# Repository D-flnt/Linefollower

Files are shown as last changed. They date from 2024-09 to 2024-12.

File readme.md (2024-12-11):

# LineFollower Daan Flinterman 3AMA 2024

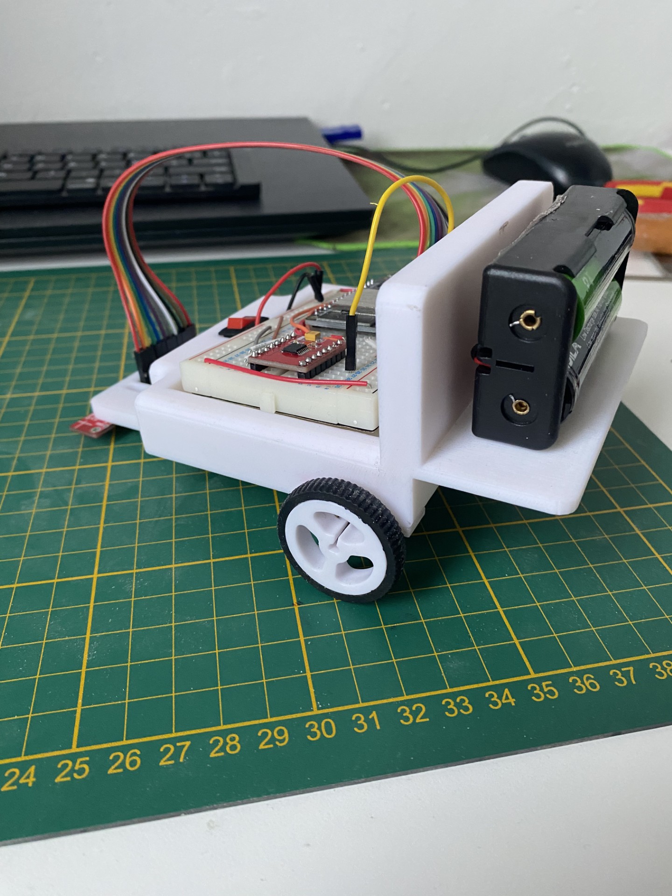
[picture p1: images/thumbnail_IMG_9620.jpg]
Mijn linefollower

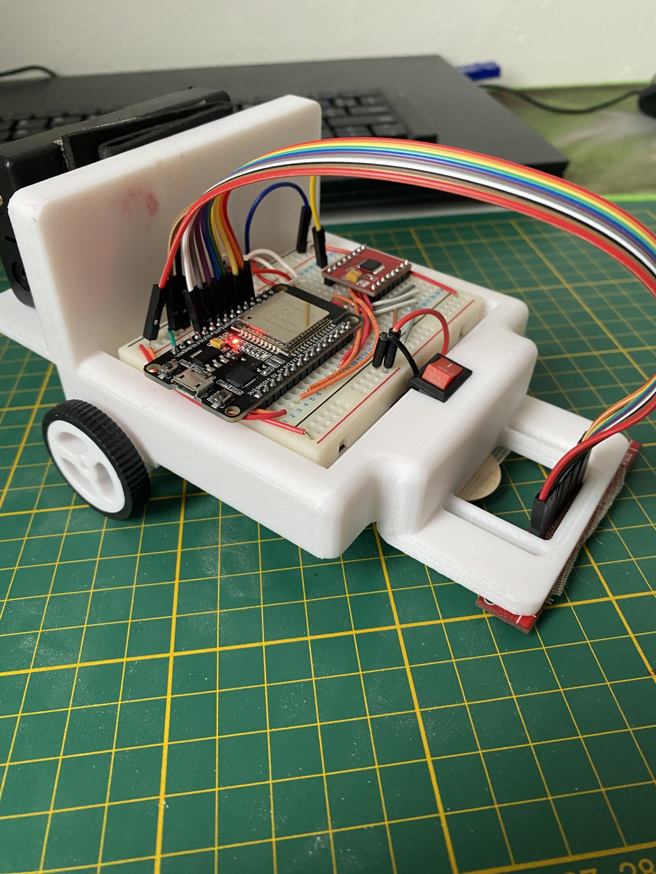
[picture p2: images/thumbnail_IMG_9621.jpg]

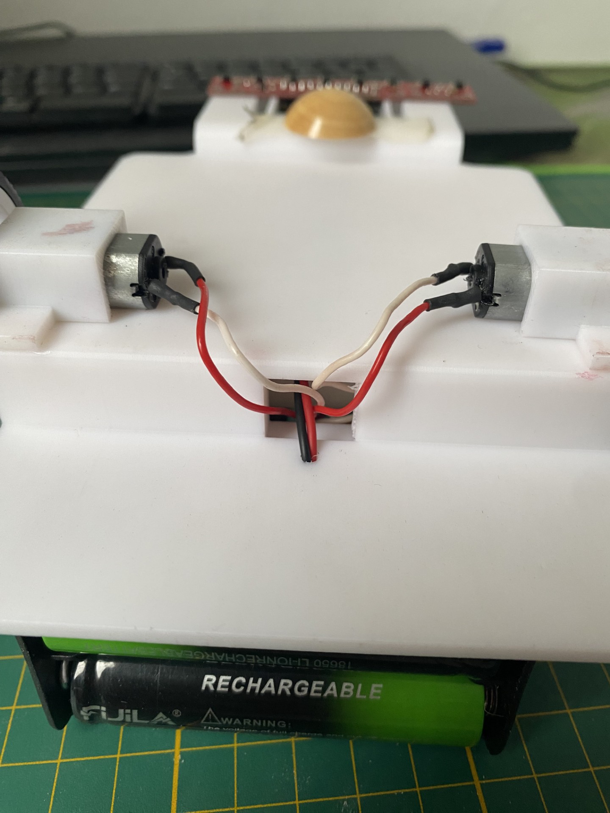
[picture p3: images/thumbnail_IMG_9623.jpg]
Onderzijde


## specifications

microcontroller: ESP32

motors: Micro Metal Gearmotor 50:1

h-bridge: DRV8833

sensors: QTR-8A Sensor Array

batteries: 2 x 18650 Li-Ion

wireless communication: Internal bluetooth module (ESP-32)

distance sensor - motors: 108mm

weight:316g

speed: 0,42m/s

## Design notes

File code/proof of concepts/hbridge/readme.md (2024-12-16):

# H-Bridge proof of concept

Minimale hard- & software die aantoont dat 2 motoren onafhankelijk van elkaar kunnen draaien, en (traploos) regelbaar zijn in snelheid en draairichting.

### Stappen:
1. Sluit de motoren aan volgens schema (OUT1, OUT2 voor motor 1, OUT3, OUT4 voor motor 2).
2. Sluit de ingangen van de H-brug volgens het schema voorzien in deze repository.
3. Sluit de **STBY** pin aan op de 3.3 V pin van de ESP-32.
4. Sluit **VCC**, **GND**, en **VM** aan volgens het schema.
5. Upload het programma en kijk of de motoren op verschillende sneleden en richtingen draaien.

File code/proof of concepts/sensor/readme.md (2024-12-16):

# Sensoren proof of concept

Minimale hard- en software die aantoont dat minimaal 6 sensoren onafhankelijk van elkaar kunnen uitgelezen worden (geen calibratie, normalisatie of interpolatie). Hierbij moet een zo groot mogelijk bereik van de AD converter benut worden (indien van toepassing).

### Stappen:
1. Zorg voor een **ESP32** en een **QTR-8 Sensor**.
2. Sluit de **VCC** pin van de sensor aan op **3.3V** van de ESP32.
3. Sluit de **GND** pin van de sensor aan op de **GND** van de ESP32.
4. Sluit de pinnen van de sensor aan volgens het schema voorzien in deze repository met de ESP 32.
5. Voorzie de ESP32 van spanning.
6. Upload het programma naar de ESP32.
7. Kijk in de seriële monitor (debugger) je zou hier de waardes van de sensoren moeten zien en de waardes zouden moeten veranderen als je je vinger voor de sensoren beweegt.

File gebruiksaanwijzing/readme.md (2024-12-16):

# Gebruiksaanwijzing

# Gebruiksaanwijzing

### opladen / vervangen batterijen
Ik heb hiervoor een oplader gekocht van aliexpress speciaal voor het type 18650 batterijen.
Maakt gebruik van een USB micro aansluiting.

### draadloze communicatie
#### verbinding maken **!ALLEEN MOGELIJK MET ANDROID**
Ik gebruik de app "serial bluetooth" met 10k reviews in de play store.
Je moet eerst in het programma declareren dat de bluetooth wordt opgestart. Hier zal je ook een naam geven aan je bluetooth module.
Als dit gebeurt is dan voorzie je de ESP-32 van stroom.
Dan verbindt je via instellingen van je android met de gegeven naam van de ESP-32.
Dan open je de APP serial bluetooth en druk je op new connection, hier duidt je weer je esp 32 aan.
Normaal gezien komt er in de terminal "connected" te staan.
Je kan nu commando's doorsturen.

#### commando's
- getPID: Vraag de huidige P, I en D waarde op.
- start: Laat de robot rijden.
- stop: Stopt de robot.
- baseSpeed[0..255]: Pas de basissnelheid aan (bij een rechte lijn)
- maxSpeed[0..255]: Pas de maximale snelheid aan (om bij te sturen)
- kp[0..]: Pas de Proportionele waarde aan.
- Ki[0..]: Pas de Integrerende waarde aan.
- Kd[0..]: Pas de Differentiërende waarde aan.

### settings
De robot rijdt stabiel met volgende parameters:
- Base speed: 95
- Max speed: 140
- Kp: 19
- Ki: 0
- Kd: 10

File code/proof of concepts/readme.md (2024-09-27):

# Proof of Concepts

Een proof of concept is een combinatie van minimale hard- en software om eenvoudig aan te tonen dat iets werkt.  
Proof of concepts kunnen enerzijds als eerste poging dienen om een bepaald onderdeel van het project werkend te krijgen. Anderzijds kunnen ze tijdens het debuggen van het finale project dienen als test om eventuele hardware problemen te elimineren bij onduidelijke problemen.
<br />  
<br />
Een proof of concept bestaat uit
* een elektronisch schema (indien van toepassing)
* minimale code om de voorop gestelde zaken te demonstreren
* minimale uitleg / aandachtspunten
<br />
De elektronische schakelingen van de proof of concepts komen bij voorkeur overeen met deze van de uiteindelijke linefollower, zodat de code zonder aanpassingen op het finale project kan draaien.

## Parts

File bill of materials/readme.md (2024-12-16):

## bill of materials
<br />

|volgnummer|naam|omschrijving|nieuw/recup|kostprijs/stuk|aantal|subtotaal|
|---|----|---|---|---|---|---|
| 1| QTR-8A Reflectance Sensor Array | This sensor module has 8 IR LED/phototransistor pairs mounted on a 0.375" pitch, making it a great detector for a line-following robot. Pairs of LEDs are arranged in series to halve current consumption, and a MOSFET allows the LEDs to be turned off for additional sensing or power-savings options. Each sensor provides a separate analog voltage output. | Nieuw | €9,95/piece | 1 | €9.95 |
| 2| Micro Metal Gear motor 1:50  | Mini N20 Reductiemotor DC 3 V-6 V 330 RPM Groot Koppel Volledig Metalen Versnellingsbak Reductiemotor 1:50 Reductieverhouding Vingerafdrukslot | Nieuw | €1.34/piece | 2  | €2,68 | 
| 3|  18650 Li-Ion battery | 2 batterijen in serie leveren bijna 8 volt. Hiermee voed ik de H-brug en de Microcontroller. | Nieuw | €2,02/piece | 2 | €4,08 |
| 4| DRV8833 H-Brug | Zal afhangend van de ingang signalen de motoren aansturen met de spanning van de batterijen. We gebruiken een H brug omdat deze makkelijker meer vermogen kan schakelen dan de Microcontroller zelf. |  Nieuw | €1,79/piece |  1 | €1,79 |
| 5| 18650 Batterij houder | Zorgt ervoor dat ik de spanning van de batterijen in serie op mn breadboard kan zetten. |  Nieuw | €1,39/piece |  1 | €1,39 |
| 6|  Tuimelschakelaar 3A  |  Een bistabiele schakelaar om de spanning van de batterijen naar het breadboard te onderbreken. | Nieuw | €0,18/piece | 10 | €1,80 |
| 7| 18650 Batterij oplader (2 sleufs) | Voor de batterijen op te laden | Nieuw | €1,92/piece | 1 |  €1.92 |
| 8|  D Gat wielen  | D gat wielen die perfect passen op de as van de reductie motor. | Nieuw | €0,39/piece |  10 | €3,89  |
| 9|  ESP-32 WROOM  | Brein van de lijnvolger (bluetooh en wifi compatable) | Nieuw | €10,00/piece | 1 | €10,00 |
| 10|  Chaussis Auto (3D printed)  |  Zorgt ervoor dat alle componenten bij elkaar worden gehouden. | Nieuw | €0,00/piece | 1 | €0,00 |
| 11| Breadboard (456 pins) | Soldeerloos breadboard om makkelijk connecties te maken tussen de componenten. | Nieuw | €9,95/piece |  1 | €9,95 |
| 12| | | | | | |

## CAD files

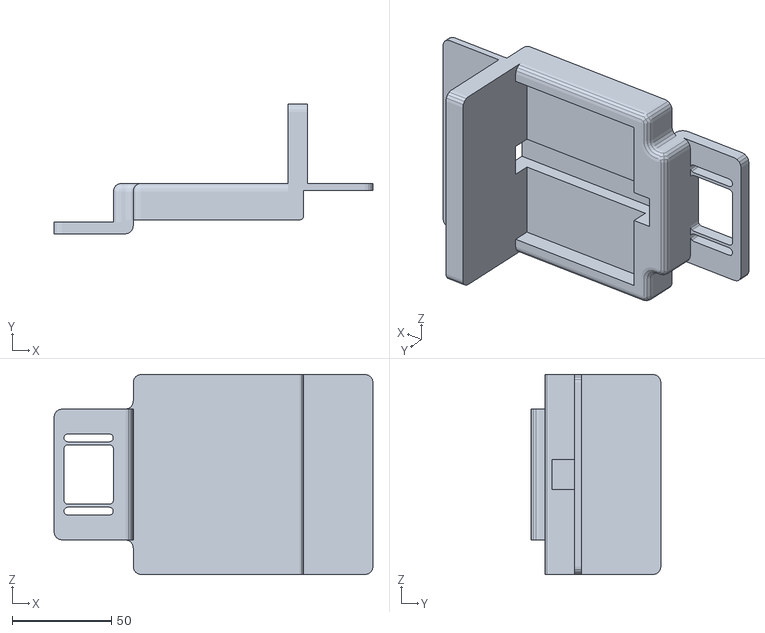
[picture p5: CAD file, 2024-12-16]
technische tekeningen/mechanisch/frame_karretje.stl
161.0 x 65.5 x 101.0

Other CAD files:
technische tekeningen/mechanisch/frame.ipt

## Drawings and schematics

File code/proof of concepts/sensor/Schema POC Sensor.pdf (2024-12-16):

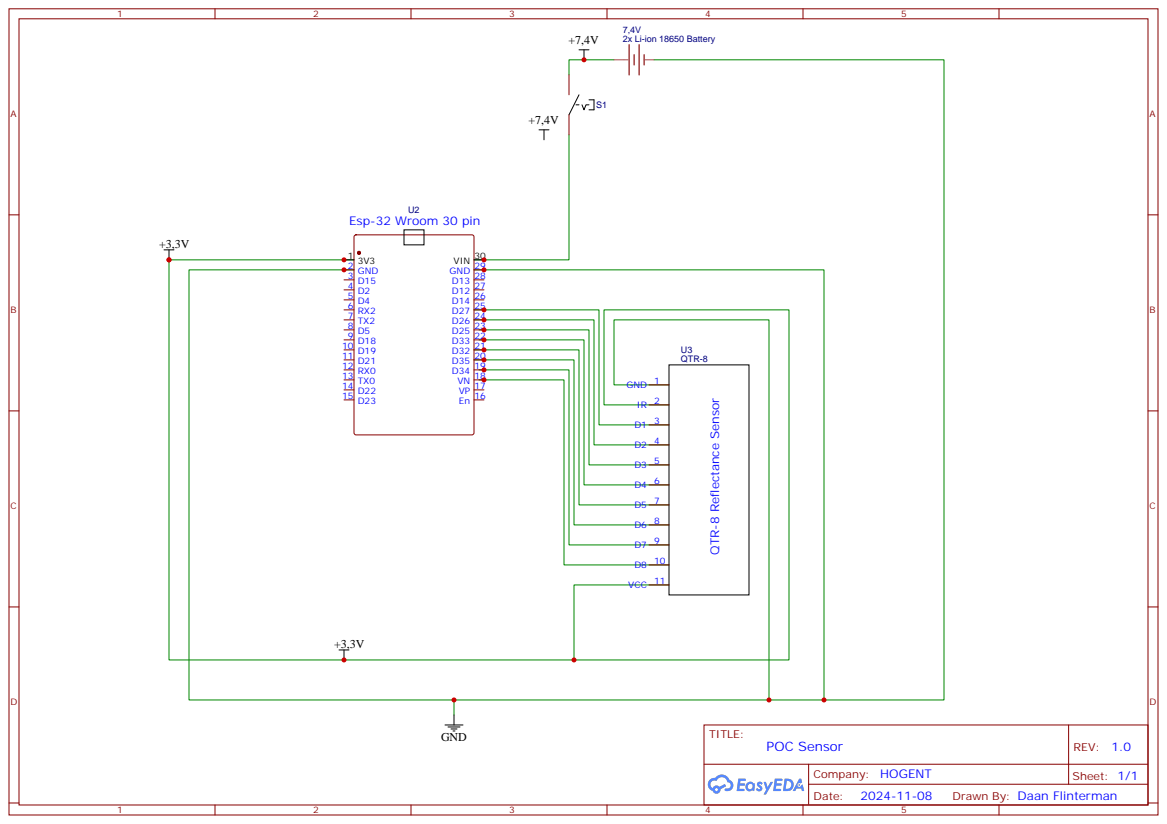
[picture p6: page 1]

Drawn By: Daan Flinterman

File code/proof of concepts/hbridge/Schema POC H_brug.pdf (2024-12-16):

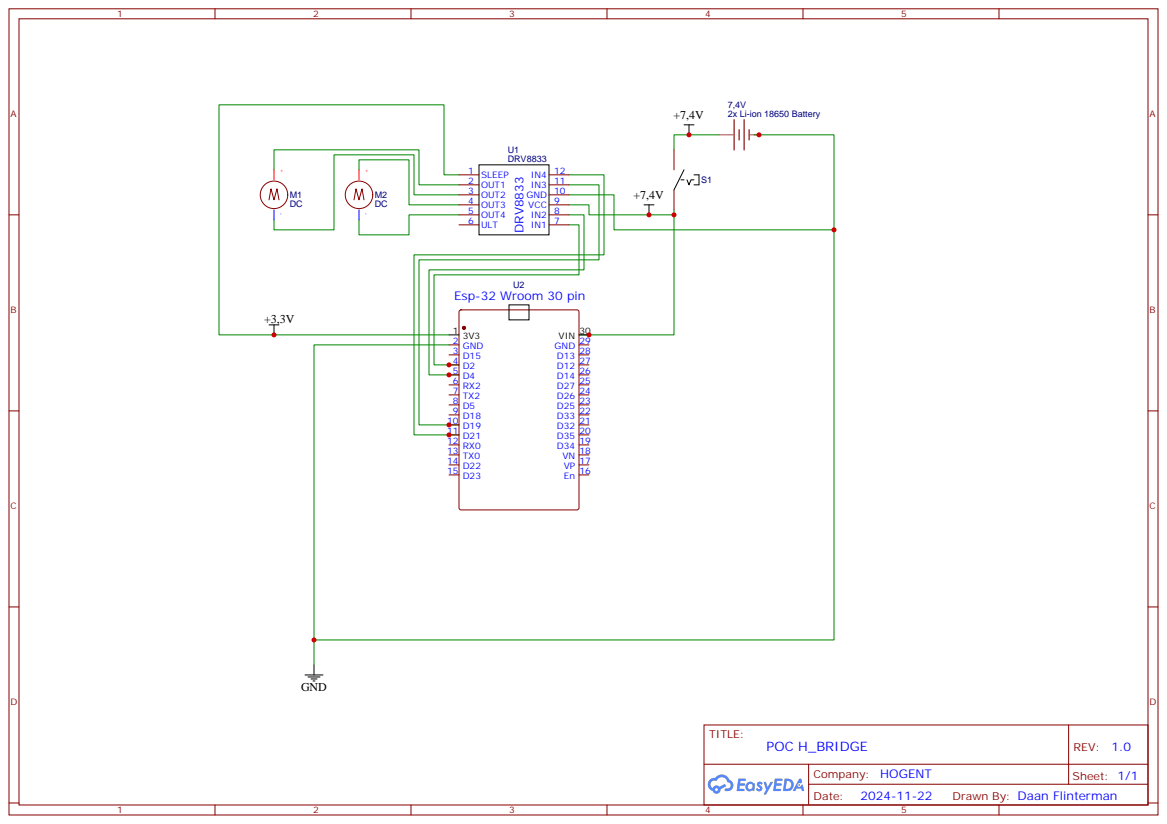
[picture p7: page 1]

Drawn By: Daan Flinterman

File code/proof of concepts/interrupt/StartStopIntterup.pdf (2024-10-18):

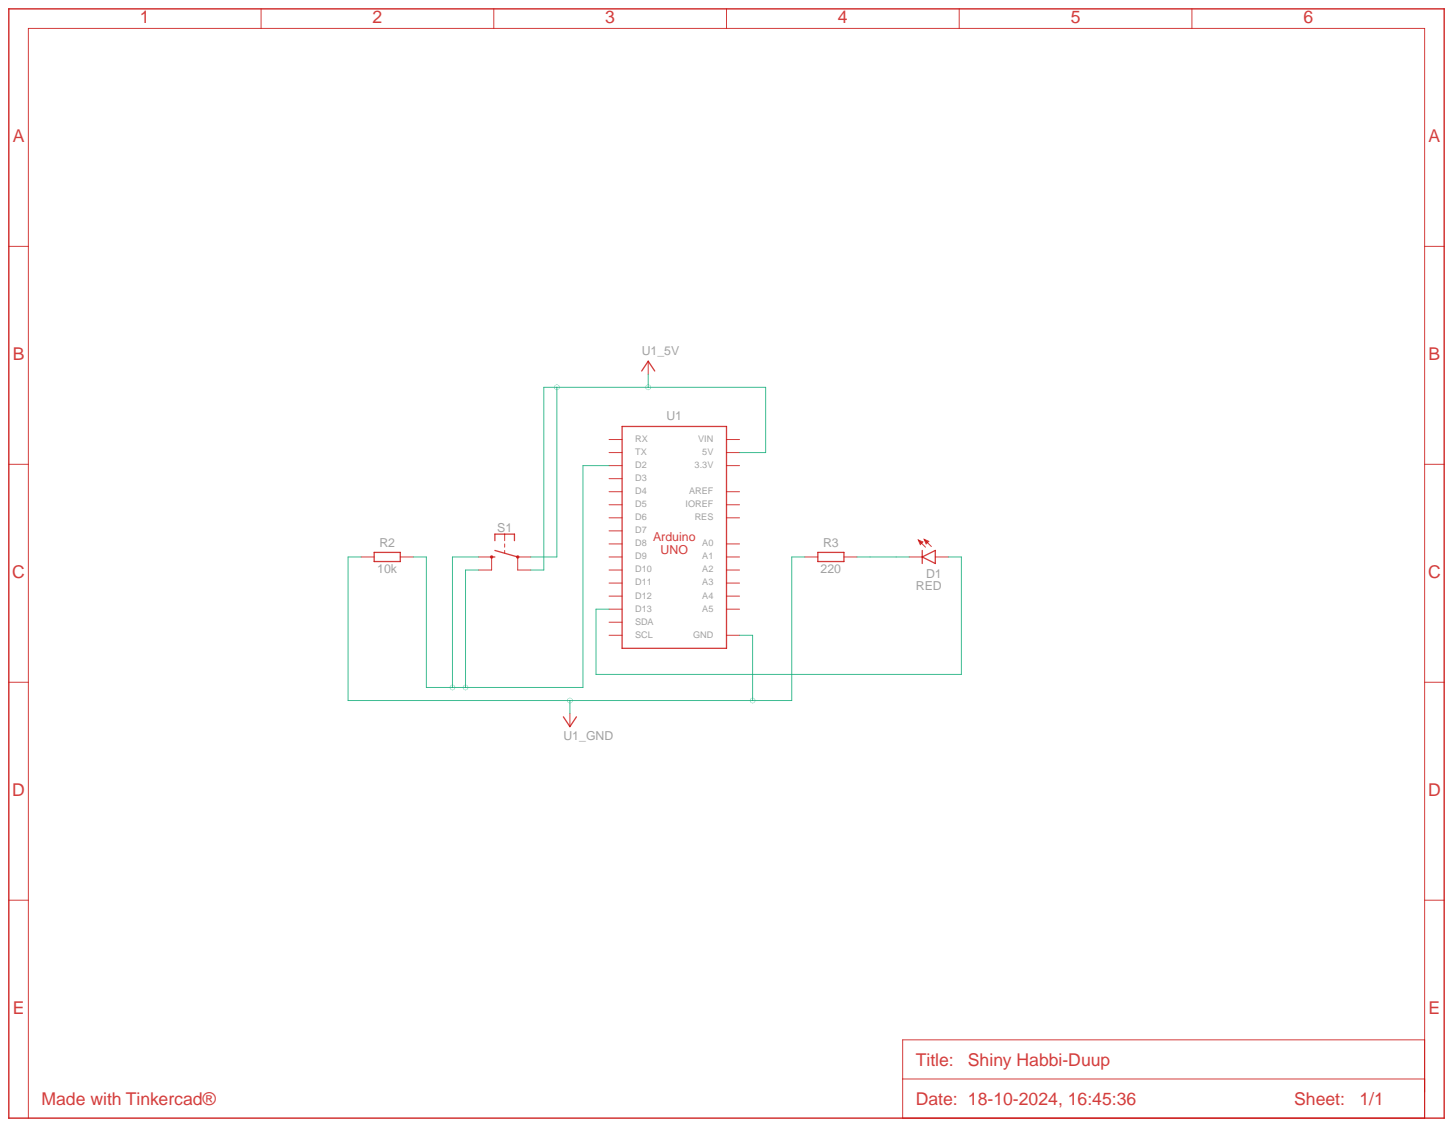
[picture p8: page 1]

Title: Shiny Habbi-Duup

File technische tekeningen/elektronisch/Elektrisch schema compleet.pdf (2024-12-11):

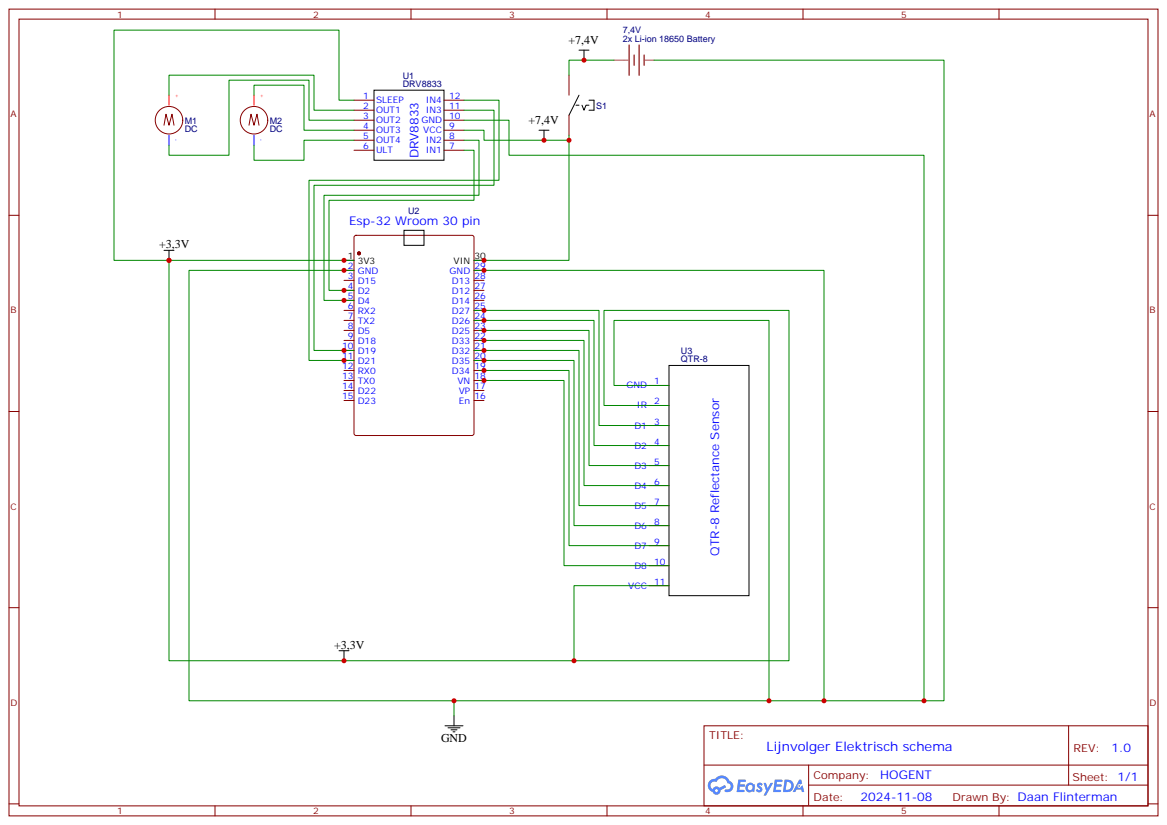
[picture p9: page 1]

Drawn By: Daan Flinterman

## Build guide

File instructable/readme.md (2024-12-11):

# Instructable

Een instructable is een stappenplan - zonder verdere uitleg - hoe je vertrekkend van de bill of materials en gebruik makend van de technische tekeningen de robot kan nabouwen. Ook de nodige stappen om de microcontroller te compileren en te uploaden staan beschreven.  

### Stap 1:
bestel alle componenten uit de bill of materials 

### Stap 2:
Test de sensoren, Gebruik de POC testcode in de repository om te controleren of de QTR-8A-sensorarray correcte waarden geeft voor zwart en wit. Controleer ook de motoren. Upload de  POC testcode om ervoor te zorgen dat beide motoren in beide richtingen correct draaien met een verschillende snelheid.

### Stap 3: Monteer de motoren en wielen
Bevestig de Micro Metal Gear Motors stevig aan het chassis.
Klik de D-gat wielen op de assen van de motoren.

### Stap 4: Plaats de batterijen en houder
Monteer de 18650 batterijhouder op het chassis.
Plaats de 18650 Li-Ion batterijen in de houder.

### Stap 5: Installeer de QTR-8A Reflectance Sensor Array
Bevestig de QTR-8A sensorarray aan de onderkant van het chassis (zie foto), zodat deze ongeveer een paar mm boven de grond hangt.

### Stap 6: Bedrading en Breadboard
Plaats het breadboard op de geschikte plaats chassis. Maak alle verbindingen tussen de batterijhouder, schakelaar, ESP32, DRV8833, en sensoren volgens het elektrisch schema te vinden in deze repository.

Tuimelschakelaar: Gebruik een bistabiele tuimelschakelaar om de stroom van de batterijhouder naar het breadboard te onderbreken. De schakelaar wordt in serie geplaatst met de positieve voedingslijn van de batterijen (tussen de + van de batterijhouder en de VCC van het breadboard). Hierdoor kun je de robot gemakkelijk in- en uitschakelen zonder de batterijen handmatig te verwijderen.

### Stap 7: Code uploaden
Download de Arduino IDE en installeer de ESP32-bibliotheek.
Compileer de code en upload deze naar de ESP32 via een USB-kabel.

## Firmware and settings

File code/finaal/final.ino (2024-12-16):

#include <BluetoothSerial.h>
BluetoothSerial SerialBT;

int motorA_IN1 = 4;
int motorA_IN2 = 2;
int motorB_IN1 = 19;
int motorB_IN2 = 21;

const int sensorPins[8] = {27, 26, 25, 33, 32, 35, 34, 39};

float Kp = 19;
float Ki = 0;
float Kd = 10;
float integral = 0;
float lastError = 0;

int baseSpeed = 95;
int maxSpeed = 140;
int leftMotorSpeed;
int rightMotorSpeed;

int sensorValues[8];
int weights[8] = {-6, -5, -4, -3, 3, 4, 5, 6};

int blackValues[8];
int whiteValues[8];

volatile bool isRunning = false;

void setup() {
  Serial.begin(115200);
  SerialBT.begin("LineFollower");
  Serial.println("Bluetooth gestart. Wacht op verbinding...");

  pinMode(motorA_IN1, OUTPUT);
  pinMode(motorA_IN2, OUTPUT);
  pinMode(motorB_IN1, OUTPUT);
  pinMode(motorB_IN2, OUTPUT);

  for (int i = 0; i < 8; i++) {
    pinMode(sensorPins[i], INPUT);
  }
}

void loop() {
  if (SerialBT.available()) {
    String command = SerialBT.readStringUntil('\n');
    processCommand(command);
  }

  if (isRunning) {
    int totalWeight = 0;
    int totalActive = 0;

    for (int i = 0; i < 8; i++) {
      sensorValues[i] = analogRead(sensorPins[i]);
      if (sensorValues[i] > 512) {
        totalWeight += weights[i] * sensorValues[i];
        totalActive += sensorValues[i];
      }
    }

    if (totalActive == 0) {
      stopMotors();
      isRunning = false;
      SerialBT.println("Robot stopped: lost the line");
      return;
    }

    int error = totalWeight / totalActive;

    integral += error;
    float derivative = error - lastError;
    float pidOutput = Kp * error + Ki * integral + Kd * derivative;

    leftMotorSpeed = baseSpeed - pidOutput;
    rightMotorSpeed = baseSpeed + pidOutput;

    leftMotorSpeed = constrain(leftMotorSpeed, -maxSpeed, maxSpeed);
    rightMotorSpeed = constrain(rightMotorSpeed, -maxSpeed, maxSpeed);

    if (leftMotorSpeed >= 0) {
      analogWrite(motorA_IN1, leftMotorSpeed);
      digitalWrite(motorA_IN2, LOW);
    } else {
      analogWrite(motorA_IN1, -leftMotorSpeed);
      digitalWrite(motorA_IN2, HIGH);
    }

    if (rightMotorSpeed >= 0) {
      analogWrite(motorB_IN1, rightMotorSpeed);
      digitalWrite(motorB_IN2, LOW);
    } else {
      analogWrite(motorB_IN1, -rightMotorSpeed);
      digitalWrite(motorB_IN2, HIGH);
    }

    lastError = error;
    delay(5);
  }
}

void processCommand(String command) {
  command.trim();
  
  if (command.startsWith("Kp")) {
    Kp = command.substring(2).toFloat();
    SerialBT.println("Kp set to: " + String(Kp));
  } else if (command.startsWith("Ki")) {
    Ki = command.substring(2).toFloat();
    SerialBT.println("Ki set to: " + String(Ki));
  } else if (command.startsWith("Kd")) {
    Kd = command.substring(2).toFloat();
    SerialBT.println("Kd set to: " + String(Kd));
  } else if (command.startsWith("baseSpeed")) {
    baseSpeed = command.substring(9).toInt();
    SerialBT.println("Base Speed set to: " + String(baseSpeed));
  } else if (command.startsWith("maxSpeed")) {
    maxSpeed = command.substring(8).toInt();
    SerialBT.println("Max Speed set to: " + String(maxSpeed));
  } else if (command.equals("getPID")) {
    SerialBT.println("Current PID: Kp=" + String(Kp) + " Ki=" + String(Ki) + " Kd=" + String(Kd));
  } else if (command.equals("getSpeed")) {
    SerialBT.println("Current Speeds: Base=" + String(baseSpeed) + " Max=" + String(maxSpeed));
  } else if (command.equals("start")) {
    isRunning = true;
    SerialBT.println("Robot started");
  } else if (command.equals("stop")) {
    isRunning = false;
    stopMotors();
    SerialBT.println("Robot stopped");
  } else if (command.startsWith("calibrate")) {
    onCalibrate(command);
  } else {
    SerialBT.println("Unknown command: " + command);
  }
}

void stopMotors() {
  analogWrite(motorA_IN1, 0);
  digitalWrite(motorA_IN2, LOW);
  analogWrite(motorB_IN1, 0);
  digitalWrite(motorB_IN2, LOW);
}

void onCalibrate(String command) {
  command.trim();
  if (command.startsWith("calibrate black")) {
    SerialBT.println("Calibrating black...");
    for (int i = 0; i < 8; i++) {
      blackValues[i] = analogRead(sensorPins[i]);
    }
    SerialBT.println("Black calibration done.");
  } else if (command.startsWith("calibrate white")) {
    SerialBT.println("Calibrating white...");
    for (int i = 0; i < 8; i++) {
      whiteValues[i] = analogRead(sensorPins[i]);
    }
    SerialBT.println("White calibration done.");
  }
}

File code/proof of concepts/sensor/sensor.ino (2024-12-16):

int sensorValue1;
int sensorValue2;
int sensorValue3;
int sensorValue4;
int sensorValue5;
int sensorValue6;
int sensorValue7;
int sensorValue8;

const int sensorPin1 = 27;
const int sensorPin2 = 26;
const int sensorPin3 = 25;
const int sensorPin4 = 33;
const int sensorPin5 = 32;
const int sensorPin6 = 35;
const int sensorPin7 = 34;
const int sensorPin8 = 39;

void setup() {
  Serial.begin(9600);
}

void loop() {
  sensorValue1 = map(analogRead(sensorPin1), 0, 4095, 1023, 0);
  sensorValue2 = map(analogRead(sensorPin2), 0, 4095, 1023, 0);
  sensorValue3 = map(analogRead(sensorPin3), 0, 4095, 1023, 0);
  sensorValue4 = map(analogRead(sensorPin4), 0, 4095, 1023, 0);
  sensorValue5 = map(analogRead(sensorPin5), 0, 4095, 1023, 0);
  sensorValue6 = map(analogRead(sensorPin6), 0, 4095, 1023, 0);
  sensorValue7 = map(analogRead(sensorPin7), 0, 4095, 1023, 0);
  sensorValue8 = map(analogRead(sensorPin8), 0, 4095, 1023, 0);

  Serial.print("Sensorwaarden: ");
  Serial.print(sensorValue1); Serial.print(" ");
  Serial.print(sensorValue2); Serial.print(" ");
  Serial.print(sensorValue3); Serial.print(" ");
  Serial.print(sensorValue4); Serial.print(" ");
  Serial.print(sensorValue5); Serial.print(" ");
  Serial.print(sensorValue6); Serial.print(" ");
  Serial.print(sensorValue7); Serial.print(" ");
  Serial.print(sensorValue8); Serial.println();

  delay(100);
}
